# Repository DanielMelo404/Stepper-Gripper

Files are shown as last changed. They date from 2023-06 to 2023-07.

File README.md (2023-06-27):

# Stepper-Gripper
Three fingers gripper with stepper motor


\section{Estado del arte - BCI:}
Una interfaz cerebro-computador es el conjunto de hardware y software que permite controlar dispositivos externos con señales cerebrales \cite{RAMADAN201726}.
El origen de este campo de investigación sucede en 1924 con Berger, el cual hace el primer grabado de señales por electro encefalografia (EEG), e identifica el patrón oscilatorio, con las ondas alpha (8-13Hz).

\section{Objetivos actuales del campo:}
\begin{itemize}
    \item Mejorar la calidad de vida de personas con heridas o enfermedades que afectan su sistema nervioso.
    \item Conectar a los seres humanos con la inteligencia artificial con el objetivo de que esta no nos deje atrás (Neuralink).
\end{itemize}

\section{Diseño}

\subsection{Requerimientos funcionales}

\begin{enumerate}
    \item Poder ser controlada remotamente
    \begin{enumerate}[label*=\arabic*.]
        \item Debe poder conectarse facilmente con plataformas que la puedan controlar \\
        \textbf{DP: Node-red}
        \item Poder conectarse a internet \\
        \textbf{DP: ESP32 WROOM}
    \end{enumerate}
    \item Poder sujetar objetos de distintos tamaños
    \textbf{DP: Motor acoplado a tornillo de potencia que mueve axialmente al hexagono de presion}
    \begin{enumerate}[label*=\arabic*.]
        \item Poder sostener una fuerza de 20N para sujetar al objeto.\\
        \textbf{DP: El motor, junto al sistema de transmisión de potencia}
        \item Se debe poder controlar la posición de la mano en su rango de movimiento con una precision suficiente como para ejercer presion sobre los objetos en su rango de sujeción.\\
        \textbf{DP: Motor stepper que con definición de 200 pasos por vuelta}
        \item Debe permitir mover el hexágono de presión linealmente sobre su recorrido.\\
        \textbf{DP: Eje de motor acoplado a tornillo de potencia cuyo carro esta sujeto al hexágono de presión}
        \begin{enumerate}[label*=\arabic*.]
            \item Debe sujetar al motor rotatoriamente sobre su eje, ejerciendo un apoyo para que el motor ejerza su torque.\\
            \textbf{DP: Hexagono acrilico en la base del motor} 
            \item Debe sujetar al motor y al sistema axialmente para que sobre el se delice el hexagono de presion y sin ejercer un troque en contra que trabe al motor.\\
            \textbf{DP: Rodamiento de sujeción axial que encaja en escalon en la parte superior final del eje}
            
        \end{enumerate}
        
    \end{enumerate}
    \item El diseño debe ser usable

    \textbf{DP: Interfaz de usuario de node-red (dashboard) e instrucciones de uso}
    \item El diseño debe ser repetible
    \textbf{DP: Repositorio con los archivos necesarios para reproducción y el informe del presente documento}
\end{enumerate}

\section{Análisis geométrico del mecanismo:}
El mecanismo esta conformado por 3 mecanismos de 4 barras. Los 3 se controlan por medio de dos eslabones y una pieza triangular al hexágono de presión, el cual tiene un recorrido de 3cm desde la posición superior hacia abajo. Esta conexión hace girar alrededor de su eje pinado al eslabón de entrada del mecanismo de 4 barras y por medio de esto logra su movimiento.

El eslabón biela (el que se sujeta en sus extremos a los eslabones que giran alrededor de sus conexiones pinadas) del mecanismo es la misma pata de agarre que sujeta al objeto. 
Al transladarse por el movimiento axial del hexagono presion, este eslabon dismuye su "altura" y se cierra sobre la posicion de agarre. De esta manera sujeta al objeto.

\subsection{Análisis relativo a la mano humana} 

Cutkosky, basándose en el trabajo de Napier, desarrollo una clasificacion de movimientos funcionalmente estudiando las poses de las manos de maquinistas en operaciones de manufactura. Segun Napier, la mano adquiere una posicion deacuerdo a lo que quiere lograr con el objeto. 

La poses de la mano se clasifican entonces posiciones de potencia y de precisión.

El mecanismo esta diseñado para permitir efectuar2 posiciones de precisión: trípode y esférica.

En lo seres humanos, el agarre trípode se utiliza para elevar objetos pequeños, pues es preciso. Además, los 3 dedos virtuales que componen el agarre permiten ejercer 3 puntos fuerza lateral y momentos, los cual lo hace ideal para sujetar el movimiento de un objeto en una trayectoria cuyas fuerzas están en dirección alrededor de los 360 grados del gripper. Un ejemplo en humanos de esta tarea es la escritura con lápiz o desenroscar un objeto sosteniendolo de 3 lugares con los dedos.

El agarre esferico tambien forma parte de los agarres de potencia. Por medio de tener un punto de apoyo directo en el marco de la maquina (o en el efector de mayor potencia como el braso en el caso humano), el movimiento realizado ahora puede involucrar mucha mayor fuerza, pues los dedos que rodean al objeto no estan haciendo empuje sino que estan haciendo fuerza en direccion radial para sujetar al objeto. De esta manera, se puede controlar el movimiento de un objeto con mayor potencia que con el agarre de tripode.

Ambos agarres también tienen la ventaja de permitir el agarre de objetos de distintas formas y tamaños, pues no solo se pueden sujetar objetos esfericos o cilindricos sino tambien objetos rectangulares o de forma irregular.

Solo con realizar un cambio en la posicion de sujecion en node-red, se puede ajustar el mecanismo para sujetar distintos objetos. 

%uso de iot: Recibir datos de utilizacion del producto para saber como esta. 
% Flexibilidad: Que por medio de unos cambios pueda pasar de ser una protesis a ser un brazo para proposito de investigacion.
% O en la plataforma.

\begin{figure}[h]
    \centering
    \includegraphics[width = 7cm]{image.png}
    \caption{Orquidea que inicialmente es plana pero cambia su forma cuando entra en contacto con el agua \cite{youtube2}}
    \label{fig:my_label}
\end{figure}

\section{}

\section{KPIs de la mano:}

\subsection{Máxima carga sujetada-probeta:}
Tiene el objetivo de medir la capacidad de sujetar de la mano. Depende totalmente de la geometría del eslabón final de agarre y de el coeficiente de fricción de este con la pieza. \\

El procedimiento para se muestra a continuación. Este KPI esta medido respecto a una sola forma de probeta, con el material definido por el usuario de la mano. En este caso se utilizo un recipiente de plástico HDPE circular en el que se deposita la carga en el centro. 

\begin{enumerate}
    \item Se posiciona la mano directamente encima de la posición de agarre. De manera que solo se requiera un movimiento vertical para que la pieza quede entre las pinzas.
    \item Se baja la mano hasta la posición de sujeción en donde este el diámetro de sujeción de la probeta.
    \item Se realiza el movimiento de la mano hasta llegar a un punto cercano al objeto. Apartir de este punto, para el apriete, se realiza el movimiento del gripper con pasos discretos (enviando uno por uno). Se aprieta hasta antes de que el motor se deslice un paso. Si ya se deslizo, debe repetirse el apriete.
    \item Se eleva la mano verticalmente a una aceleración de menos de $1 cm/s^2$ hasta una altura de por lo menos 10cm.
    
\end{enumerate}

Si el anterior procedimiento fue exitoso, se toma el peso de la probeta utilizada como el valor de este KPI. Este KPI no solo consta del peso cargado sino también de la probeta utilizada (peso y forma).

Por esto se deben informar ambas informaciones al informar sobre este KPI.

\subsection{}
Este KPI busca medir la usabilidad de la mano, es decir, la facilidad con la que se puede realizar la función que desempeña. A este punto, la mano esta enfocada a poder hacer uso del sistema de actuación de la mano para hacer el testeo y verificación de este.\\
De esta forma, se define este KPI por medio de medir la cantidad de tiempo que le toma a una persona mover por primera vez la mano.

Metodología para la obtención de este KPI:

\begin{enumerate}
    \item La persona lee las instrucciones de utilización de la mano por completo.
    \item Se le indica a la persona que haga que el gripper se mueva y se toma el tiempo desde que se le indica esto hasta que mueve por primera vez la mano.
\end{enumerate}

Este KPI asume que la persona que lo utilizara es el laboratorista Juan Camilo de la universidad o cualquier persona que halla estudiado el pregardo en ingenieria Mecanica o Mecatronica que ya halla cursado los prerequisitos de la materia APM o materias equivalentes.

Tambien se asume que la persona sabe como acceder a node-red y tambien al dashboard de este.

\begin{itemize}
    \item 
\end{itemize}

\section{Gemelo digital}

El gemelo digital permite la simulación del mecanismo de la mano en su rango de movimiento. El método de reproducción de su geometría fue la medición de las medidas con calibrador con una resolución de 0.02mm. Los ángulos fueron medidos con el goniómetro disponible en el laboratorio con las medidas con una resolución de 1 grado.

\begin{figure}[h]
    \centering
    \includegraphics[width = 7cm]{twin.png}
    \caption{Gemelo digital de la mano \cite{youtube2}}
    \label{fig:my_label}
\end{figure}

Así mismo el gemelo digital se verifico al imprimir las piezas en material PLA. Se encontraron desviaciones respecto a las dimensiones principales de \pm 1.3mm.

\begin{figure}[h]
    \centering
    \includegraphics[width = 7cm]{dash.png}
    \caption{Interfaz de usuario node-red \cite{youtube2}}
    \label{fig:my_label}
\end{figure}

El gemelo digital permite la simulacion del movimiento del mecanismo, lo cual sera util para previsualizar el movimiento del actuador una vez armado.

\section{IIoT}

\subsection{Conexion wifi}

El ESP32 utiliza las credenciales de la red, nombre de la red y contraseña de esta, para conectarse al inicio de su funcionamiento.
Las credenciales se ingresan directamente en el codigo del ESP32.

\begin{figure}[h]
    \centering
    \includegraphics[width = 7cm]{wifi.png}
    \caption{Conexion wifi}
    \label{fig:my_label}
\end{figure}

\subsection{Conexion MQTT}
El esquema de conexion se puede apreciar en el diagrama POA estatico. El ESP32 se conecta gracias a la libreria PubSubClient con el broker MQTT de hive. Alli crea un topico llamado StepperDMAOut y publica a este topico. Tambien se subsribe a un topico llamado stepperDMAin, a donde se envia la posicion del actuador.    

El servidor de Node-red, instaldo en alguna raspberry-pi o computador con conexion a internet, publica la informacion de posicion del actuador al topico stepperDMAin y se subscribe al topico stepperDMAout, del mismo borker Hive.

\begin{figure}[h]
    \centering
    \includegraphics[width = 7cm]{conect.png}
    \caption{Codigo para conexion con broker}
    \label{fig:my_label}
\end{figure}

\begin{figure}[h]
    \centering
    \includegraphics[width = 7cm]{node.png}
    \caption{Diagrama de node-red utilizado para la conexion con el broker}
    \label{fig:my_label}
\end{figure}

La informacion del usuario se captura por medio de los nodos slider y numeric, los cuales representan componentes de la interfaz de usuario en el dashboard de nodered.

\begin{figure}[h]
    \centering
    \includegraphics[width = 7cm]{node.png}
    \caption{Dashboard de node-red}
    \label{fig:my_label}
\end{figure}

La conexion con el broker MQTT se realiza por medio de los nodos receptor y publicador, los cuales utilizan la informacion de la direccion del broker, el nombre de los topicos y el puerto de este para realizar la conexion.

El dato enviado desde node red es la carga paga, la cual tiene el tipo de dato payload. Al llegar y salir del borker sale con tipo byte y en el ESP 32 se realiza su conversion a char y luego a int, para asi finalmentes ser utilizada como el numero de pasos que el motor dara desde su posicion de inicio.

La posicion de inicio corresponde a 0 pasos. Por esto la posicion del hexagono de presion debe comenzar desde el principio del recorrido del tornillo de potencia, en la parte superior.

\section{Electrónica y control del motor}

El circuito se compone del ESP32 y del driver del motor stepper. Tambien se utiliza un regulador de 5V para darle poder al ESP32, un capacitor de desacople para compensar cambios de corriente bruscos, y unos leds indicadores. Las borneras se utilizan para conectar con el motor y la bornera-conector para conectar la fuente de 12V.

El control del motor se realizo por medio de los pines step y dir. Una vez conectado el driver como se oberva en la figUra \cite{4988}, el pin step se debe conectar a algun GPIO del ESP32. Puede ser cualquiera pero se utilizo el GPIO 1. Cada vez que el motor da un paso, se envia un pulso por este pin. El pin dir se utiliza para controlar la direccion del motor. Tambien se puede conectar a cualquier GPIO pero se utilizo el GPIO 3.

\begin{figure}[h]
    \centering
    \includegraphics[width = 7cm]{a4988.png}
    \caption{Esquema de conexión para el driver}
    \label{4988}
\end{figure}

El circuito se manufacturo per medio de serigrafia en PCB y los archivs de Kicad se encuentran disponbiles en el repositorio "stepper gripper" de github. 

\begin{figure}[h]
    \centering
    \includegraphics[width = 7cm]{squema.png}
    \caption{Esquematico del circuito}
    \label{fig:my_label}
\end{figure}

\begin{figure}[h]
    \centering
    \includegraphics[width = 7cm]{circu.png}
    \caption{Circuito en PCB}
    \label{fig:my_label}
\end{figure}

\section{Control del movimiento del motor}

El control de movimiento se realizo por medio de la libreria accelstepper de Arduino. 

Se debe instanciar una interfaz de stepper indicando los pines de pasos y dirección. \cite{int}

\begin{figure}[h]
    \centering
    \includegraphics[width = 7cm]{acc.png}
    \caption{Instanciación de interfaz para motor}
    \label{int}
\end{figure}

El setup del stepper se muestra en la figura \cite{in2}. 
Estos parametros se utilzran cuando sele solicite al motor alcanzar una posicion. setAcceleration configura la aceleracion para el perfil trapezoidal que siguie el stepper entre posicion y posicion. La velocidad maxima durante recorrido trapezoidal tambien se cofigura con setMaxSpeed.

setSpeed se utiliza para configurar la velocidad a la que el motor se movera cuando lo haga a velocidad constante sin aceleracion o desaceleracion.

\begin{figure}[h]
    \centering
    \includegraphics[width = 7cm]{set.png}
    \caption{Establecimiento de parámetros iniciales para motor}
    \label{int2}
\end{figure}

El motor se controla en el ciclo loop por medio del codigo de la figura \ref{in3}. Requested position es la posicion solicitada y reachingPosition es la posición a la que se esta moviendo en ese momento en particular.
Si estas son distintas, se realiza el comando moveTo, el cual interrumpe el movimiento y hace que el motor inmediatamente comience a moverse hacia la posición señalada.

\begin{figure}[h]
    \centering
    \includegraphics[width = 7cm]{mot.png}
    \caption{Establecimiento de parámetros iniciales para motor}
    \label{in3}
\end{figure}

\section{Algoritmo de clasificación de señales}

\begin{figure}[h]
    \centering
    \includegraphics[width = 7cm]{mot.png}
    \caption{Establecimiento de parámetros iniciales para motor}
    \label{in3}
\end{figure}

\begin{figure}[h]
    \centering
    \includegraphics[width = 7cm]{mot.png}
    \caption{Establecimiento de parámetros iniciales para motor}
    \label{in3}
\end{figure}

El algoritmo 

\section{Conclusiones:} \label{sec:metodologia} %10min

\begin{itemize}
    \item La manufactura aditiva es poderosa cuando es utilizada en conjunto con un gemelo digital por medio de permitir la reproducción exacta de la pieza y de esta forma desacoplando el proceso de prototipado del objeto real.
    \item Node-red facilita la conexión con protocolo MQTT con borkers, por medio de la representación intuitiva con nodos y flujos del sistema de información
    \item Los motores steppers facilitan el control de movimiento por medio de no requerir un sistema de feedback para controlar su posición y al permitir un torque sostenido.
\end{itemize}

\begin{itemize}
   
\end{itemize}

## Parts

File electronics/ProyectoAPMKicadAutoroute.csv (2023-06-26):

# | Reference | Qty | Value | Footprint | DNP
1 | C1 | 1 | 100u | Capacitor_THT:CP_Axial_L10.0mm_D6.0mm_P15.00mm_Horizontal
2 | J1, J2 | 2 | Conn_01x15_Socket | Connector_PinSocket_2.54mm:PinSocket_1x15_P2.54mm_Vertical
3 | J3, J4 | 2 | Conn_01x08_Socket | Connector_PinSocket_2.54mm:PinSocket_1x08_P2.54mm_Vertical
4 | J5, J6, J7 | 3 | Screw_Terminal_01x02 | TerminalBlock:TerminalBlock_Altech_AK300-2_P5.00mm
5 | J8 | 1 | PicKit | Connector_PinHeader_2.54mm:PinHeader_1x05_P2.54mm_Vertical
6 | J9 | 1 | PicKit | Connector_PinHeader_2.54mm:PinHeader_1x01_P2.54mm_Vertical
7 | R1, R2 | 2 | 330 | Resistor_THT:R_Axial_DIN0204_L3.6mm_D1.6mm_P7.62mm_Horizontal
8 | U1 | 1 | LM7805_TO220 | Package_TO_SOT_THT:TO-220-3_Horizontal_TabDown

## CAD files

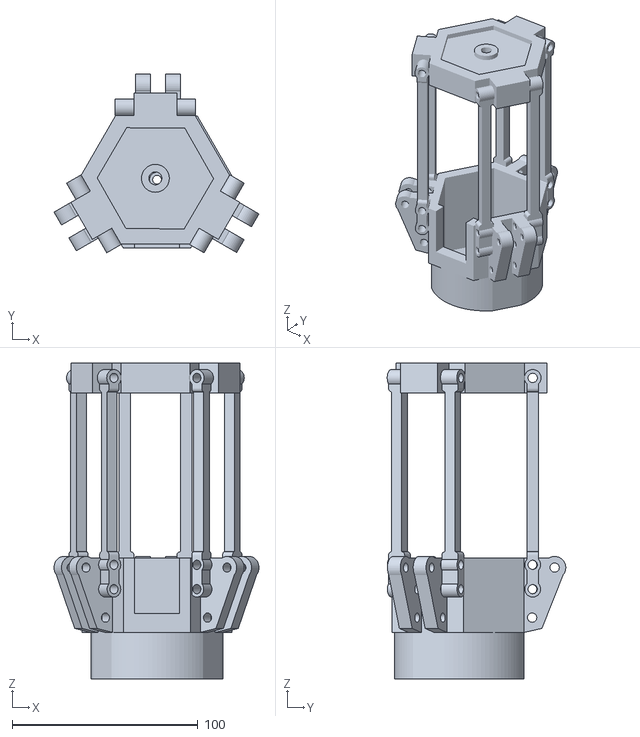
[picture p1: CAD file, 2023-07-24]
3D models/STLfiles/marco_ensamblado.stl
110.2 x 96.0 x 169.9

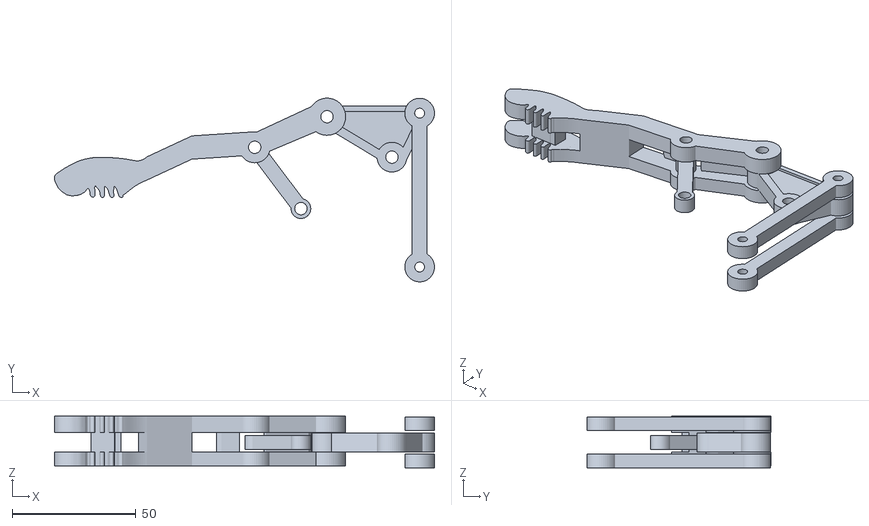
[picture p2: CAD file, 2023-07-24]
3D models/STLfiles/subensamble_patas.stl
153.4 x 74.2 x 20.9

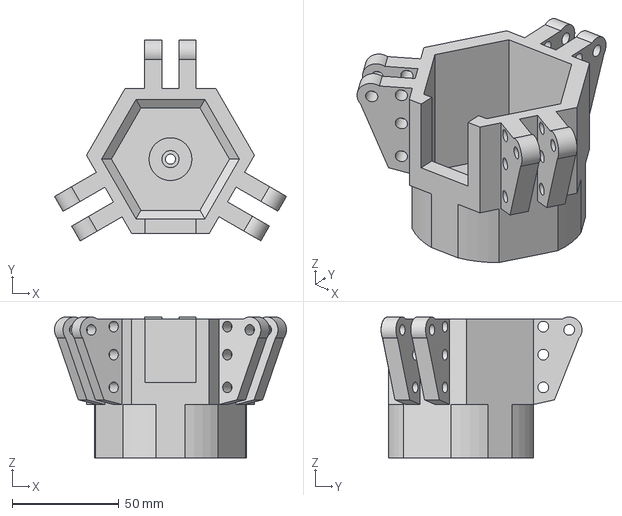
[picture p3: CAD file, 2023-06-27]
3D models/Marco v13.step
108.5 x 94.0 x 65.9 mm

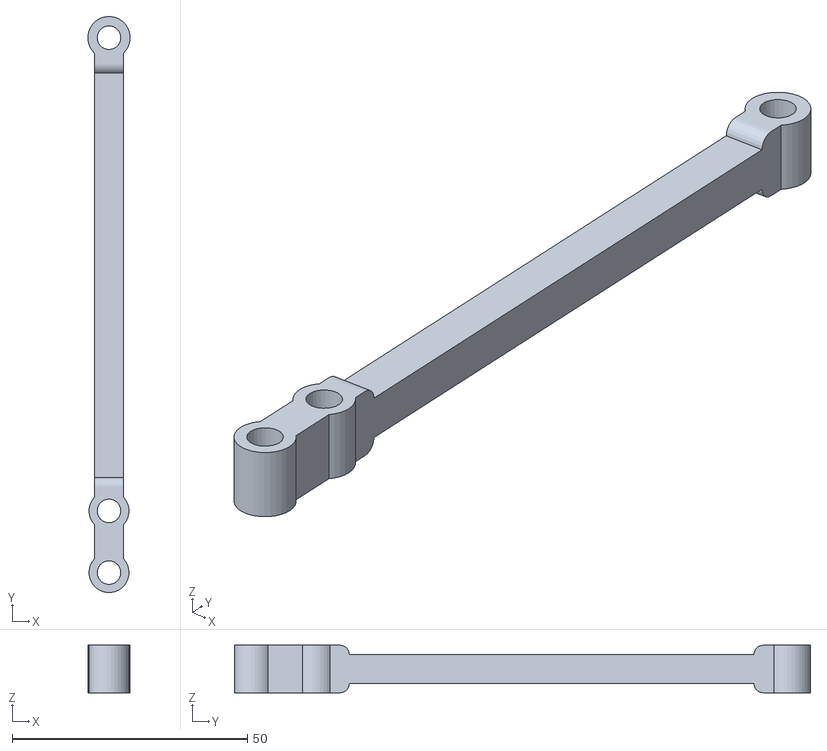
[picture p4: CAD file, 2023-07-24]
3D models/STL_en_metros/Barra_marco_en_m.stl
8.97 x 122.3 x 10.1

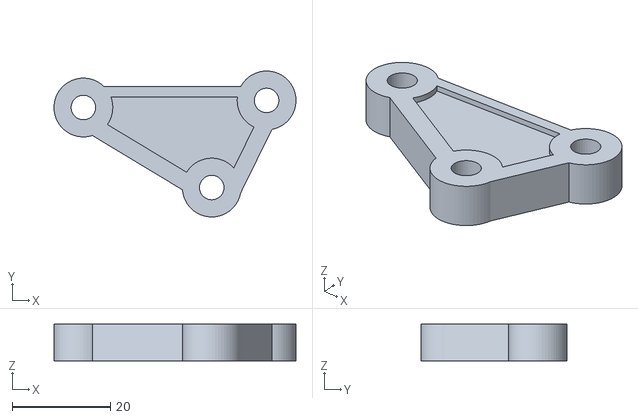
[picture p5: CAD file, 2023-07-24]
3D models/STLfiles/triangulo.stl
49.4 x 29.8 x 7.50

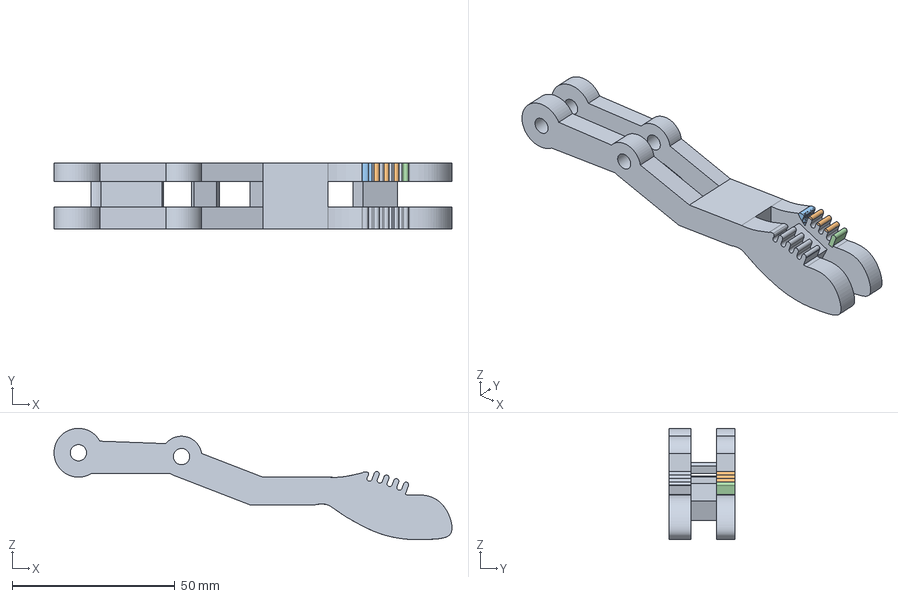
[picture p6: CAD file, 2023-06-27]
3D models/Pata de agarre (v14~recovered).step
122.3 x 20.1 x 34.2 mm

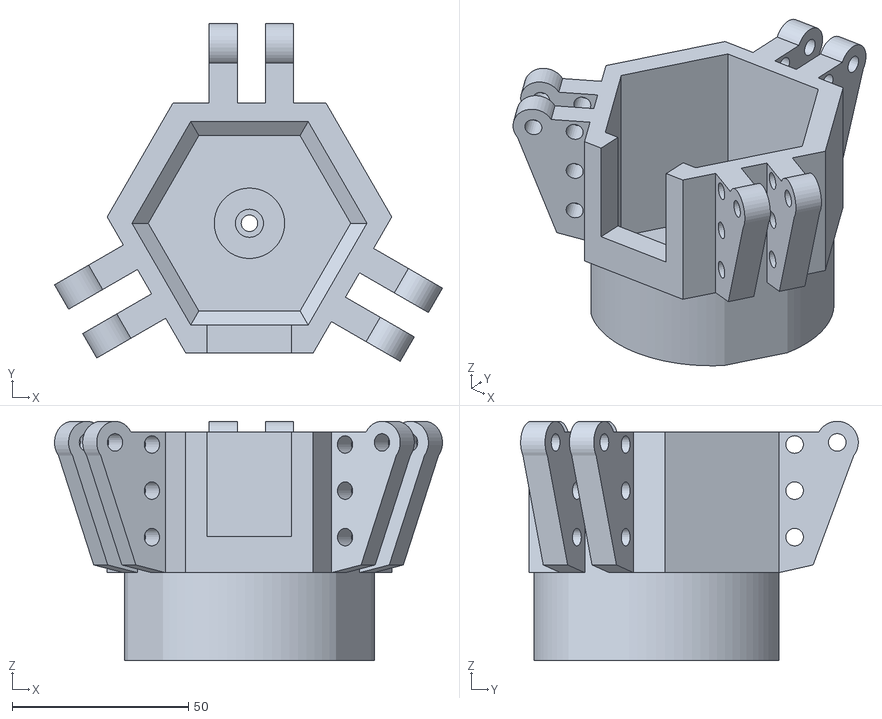
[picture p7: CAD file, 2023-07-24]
3D models/STLfiles/Marco.stl
110.2 x 95.9 x 68.0

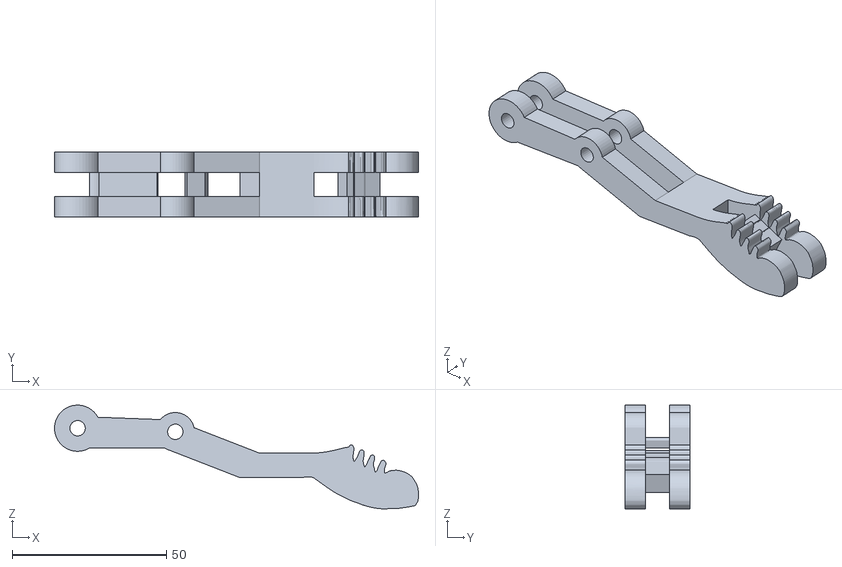
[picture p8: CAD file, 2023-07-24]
3D models/STLfiles/Pata_de_agarre.stl
118.0 x 21.2 x 33.6

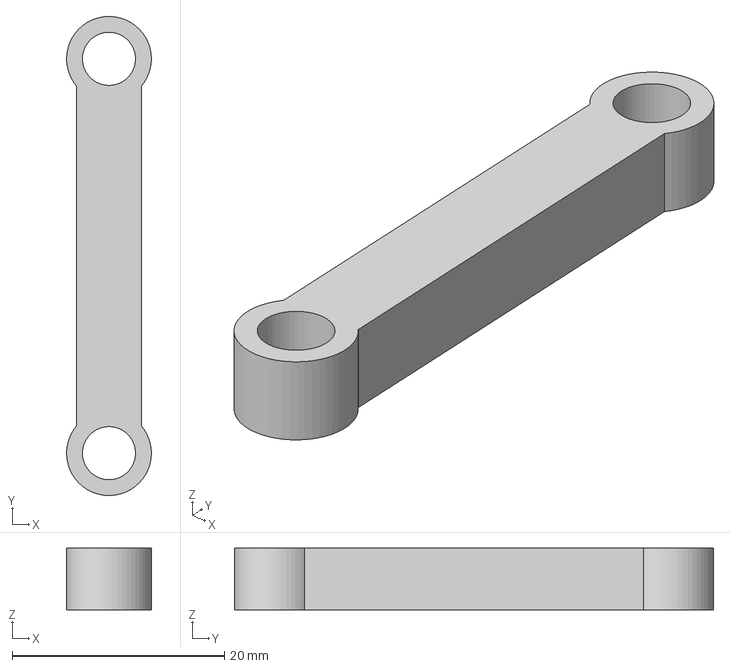
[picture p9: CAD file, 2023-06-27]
3D models/Eslabon pequeño v5.step
8.00 x 45.2 x 5.80 mm

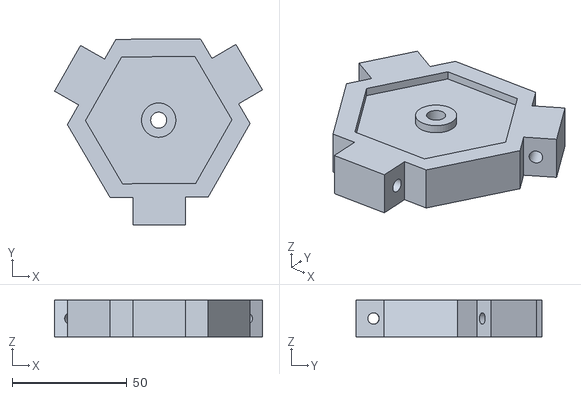
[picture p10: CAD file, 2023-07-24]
3D models/STLfiles/Hexagono_superior.stl
90.8 x 81.4 x 16.0

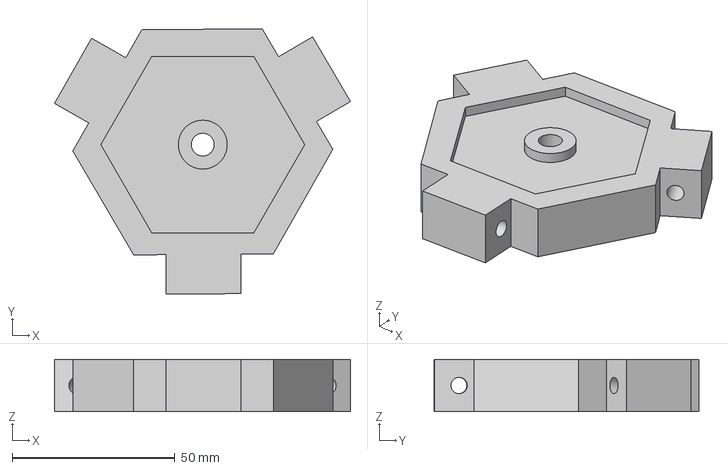
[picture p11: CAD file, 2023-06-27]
3D models/Hexagono superior con rodamiento v12.step
90.8 x 81.4 x 16.0 mm

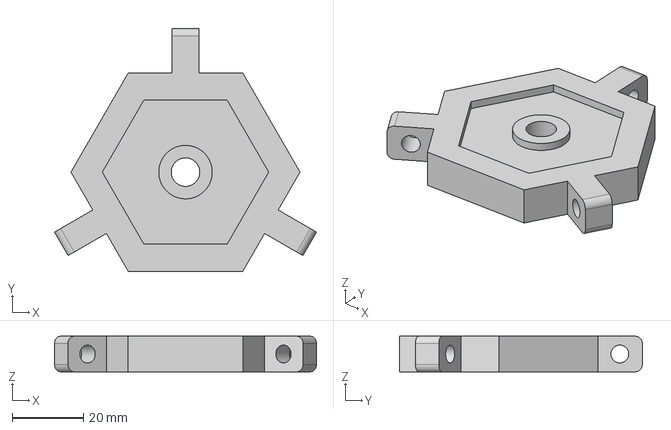
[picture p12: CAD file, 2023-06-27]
3D models/Hexagono de presion original v1.step
73.4 x 68.0 x 10.0 mm

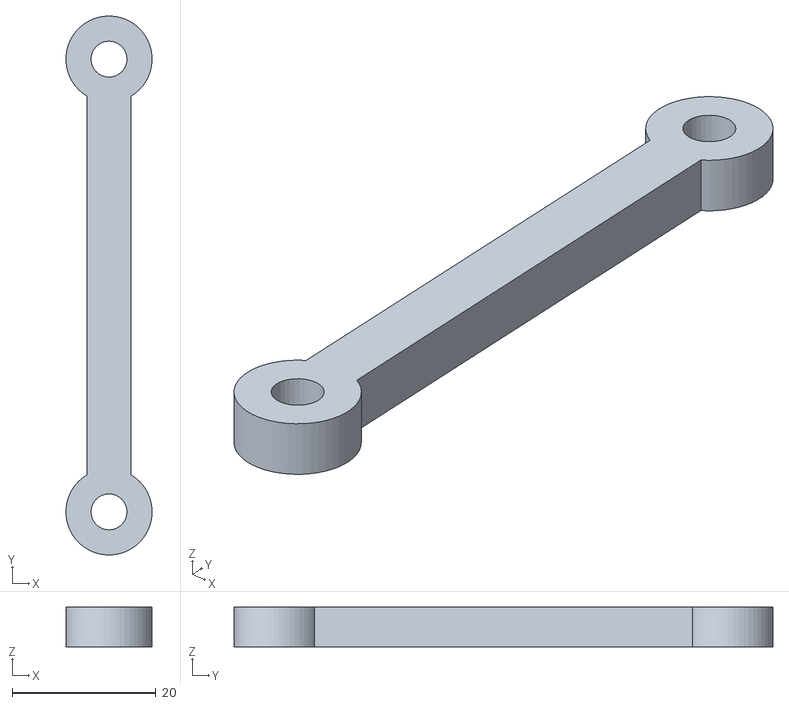
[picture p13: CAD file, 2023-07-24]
3D models/STLfiles/Eslabon_esbelto.stl
12.0 x 75.0 x 5.50

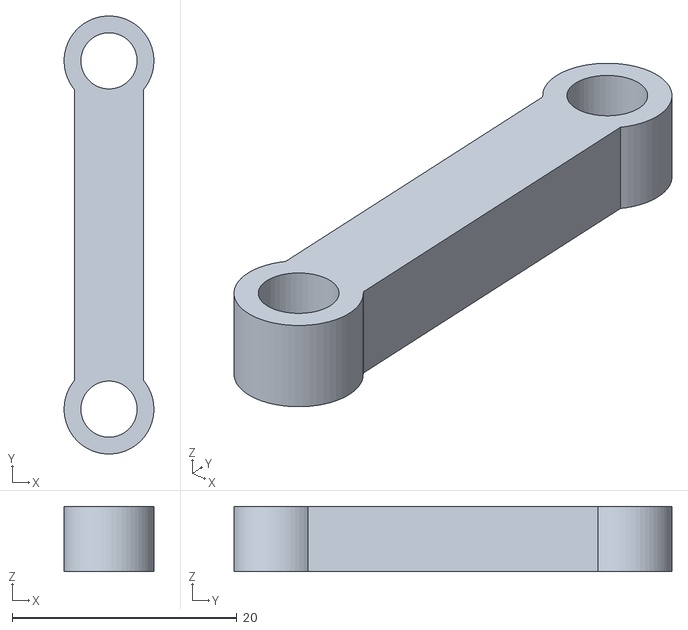
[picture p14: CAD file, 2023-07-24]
3D models/STLfiles/Eslabon_pequeño.stl
7.99 x 39.0 x 5.80

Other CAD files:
3D models/Barra marco v8.step
3D models/STLfiles/Hexagono_de_presion.stl
3D models/ensamble v16.f3z

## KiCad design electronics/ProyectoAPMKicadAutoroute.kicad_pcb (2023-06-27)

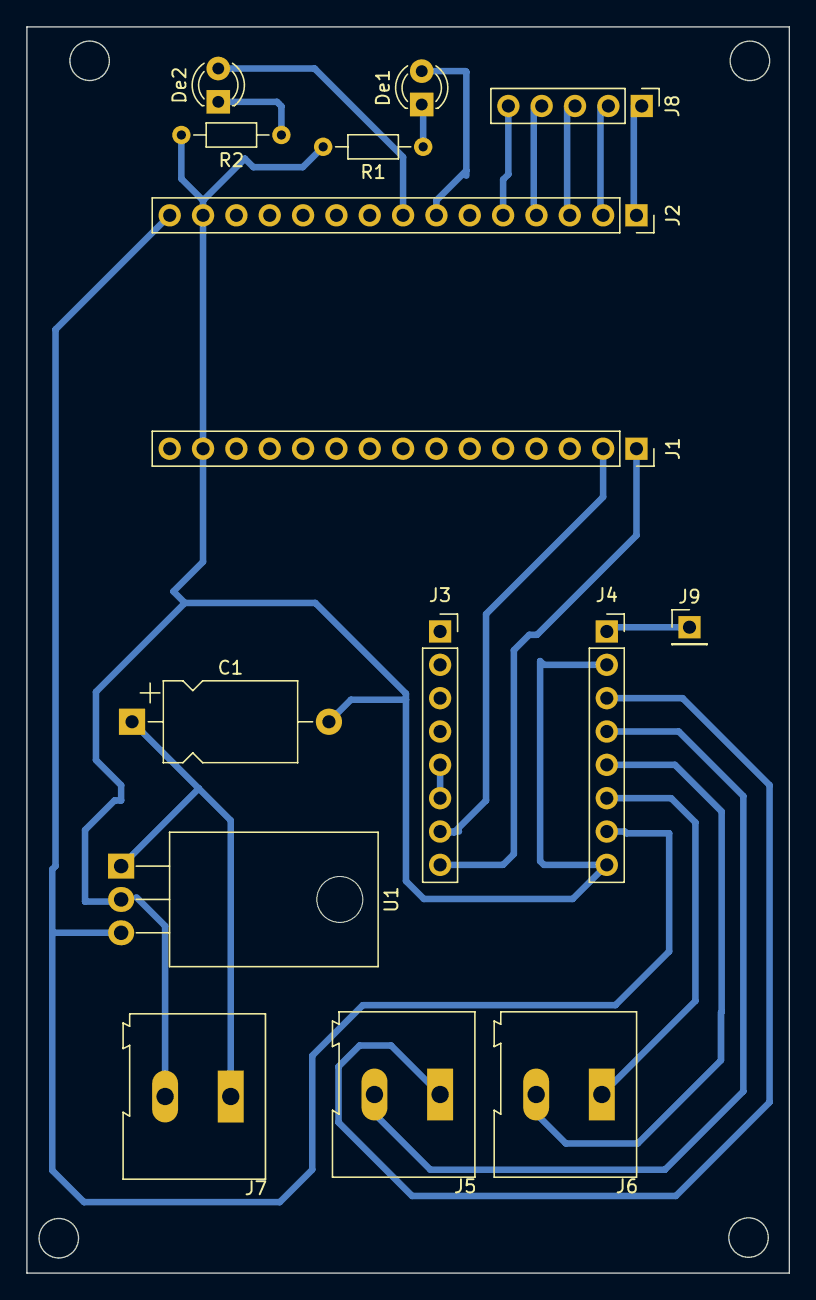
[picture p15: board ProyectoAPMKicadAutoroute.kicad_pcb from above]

Board: 2 copper layers, 58.1 x 94.9 mm, 15 parts (0 on the bottom side), 20 nets.

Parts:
C1: 100u; CP_Axial_L10.0mm_D6.0mm_P15.00mm_Horizontal
De1, De2: LED; LED_D3.0mm_Clear
J1, J2: Conn_01x15_Socket; PinSocket_1x15_P2.54mm_Vertical
J3, J4: Conn_01x08_Socket; PinSocket_1x08_P2.54mm_Vertical
J5, J6, J7: Screw_Terminal_01x02; TerminalBlock_Altech_AK300-2_P5.00mm
J8: PicKit; PinHeader_1x05_P2.54mm_Vertical
J9: PicKit; PinHeader_1x01_P2.54mm_Vertical
R1, R2: 330; R_Axial_DIN0204_L3.6mm_D1.6mm_P7.62mm_Horizontal
U1: LM7805_TO220; TO-220-3_Horizontal_TabDown

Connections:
12V+: C1.1, J7.1, U1.1 (VI)
GND: C1.2, J1.14, J2.14, J4.2, J4.8, J7.2, R1.2, R2.2, U1.2 (GND)
unnamed: De1.2 (A), J2.7
unnamed: De1.1 (K), R1.1
unnamed: De2.2 (A), J2.8
unnamed: De2.1 (K), R2.1
unnamed: J2.1, J8.1
unnamed: J2.2, J8.2
unnamed: J2.3, J8.3
unnamed: J2.4, J8.4
unnamed: J2.5, J8.5
unnamed: J3.5, J3.6
unnamed: J4.1, J9.1
unnamed: J4.3, J5.1
unnamed: J4.4, J5.2
unnamed: J4.5, J6.2
unnamed: J4.6, J6.1
VDD: J2.15, J4.7, U1.3 (VO)
dir: J1.1, J3.8
step: J1.2, J3.7

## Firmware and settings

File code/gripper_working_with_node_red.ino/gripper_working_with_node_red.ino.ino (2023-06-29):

/*
 Basic ESP8266 MQTT example
 This sketch demonstrates the capabilities of the pubsub library in combination
 with the ESP8266 board/library.
 It connects to an MQTT server then:
  - publishes "hello world" to the topic "outTopic" every two seconds
  - subscribes to the topic "inTopic", printing out any messages
    it receives. NB - it assumes the received payloads are strings not binary
  - If the first character of the topic "inTopic" is an 1, switch ON the ESP Led,
    else switch it off
 It will reconnect to the server if the connection is lost using a blocking
 reconnect function. See the 'mqtt_reconnect_nonblocking' example for how to
 achieve the same result without blocking the main loop.
 To install the ESP8266 board, (using Arduino 1.6.4+):
  - Add the following 3rd party board manager under "File -> Preferences -> Additional Boards Manager URLs":
       http://arduino.esp8266.com/stable/package_esp8266com_index.json
  - Open the "Tools -> Board -> Board Manager" and click install for the ESP8266"
  - Select your ESP8266 in "Tools -> Board"
*/
#include <stdlib.h>
#include <WiFi.h>
#include <PubSubClient.h>
#include <AccelStepper.h>
#define BUILTIN_LED 2


const int dirPin = 1;
const int stepPin = 3;
//const int en = 3;
const int ms1 = 21;
const int ms2 = 19;
const int ms3 = 18;
const int reset = 5;
const int sleepPin = 17;


void setupPins(){
//  digitalWrite(en, LOW);
  digitalWrite(ms1, LOW);
  digitalWrite(ms2, LOW);
  digitalWrite(ms3, LOW);
  digitalWrite(reset, HIGH);
  digitalWrite(sleepPin, HIGH);
//  digitalWrite(en, LOW);
}

int requestedPosition =0;
int reachingPosition = 0;

// Define motor interface type
#define motorInterfaceType 1

AccelStepper myStepper(motorInterfaceType, stepPin, dirPin);

// Update these with values suitable for your network.

const char* ssid = "wifiName";
const char* password = "wifiPassword";

const char* mqtt_server = "broker.hivemq.com";

WiFiClient espClient;
PubSubClient client(espClient);
unsigned long lastMsg = 0;
#define MSG_BUFFER_SIZE  (50)
char msg[MSG_BUFFER_SIZE];
int value = 0;

void setup_wifi() {

  delay(10);
  // We start by connecting to a WiFi network
  Serial.println();
  Serial.print("Connecting to ");
  Serial.println(ssid);
  WiFi.mode(WIFI_STA);
  WiFi.begin(ssid, password);

  while (WiFi.status() != WL_CONNECTED) {
    delay(500);
//    Serial.print(".");
  }

  randomSeed(micros());

//  Serial.println("");
//  Serial.println("WiFi connected");
//  Serial.println("IP address: ");
//  Serial.println(WiFi.localIP());
}

void callback(char* topic, byte* payload, unsigned int length) {
//  Serial.print("Message arrived [");
//  Serial.print(topic);
//  Serial.print("] ");
  char pos[length];
  for (int i = 0; i < length; i++) {
    pos[i] = (char)payload[i];
//    Serial.print((char)payload[i]);
  }
  Serial.println(pos);
char *output;
    long result = strtol(pos, &output, 10) + 1;
//Serial.println((int)result);
//  requestedPosition = ((char)payload[0]-'0')*100;
requestedPosition = -1*(int)result;

//  Serial.println("requestedPosition"+(String)requestedPosition);
//Serial.println((char)payload[0]);

  
//  Serial.println();

  // Switch on the LED if an 1 was received as first character
  if ((char)payload[0] == '1') {
    digitalWrite(BUILTIN_LED, LOW);   // Turn the LED on (Note that LOW is the voltage level
    // but actually the LED is on; this is because
    // it is active low on the ESP-01)
  } else {
    digitalWrite(BUILTIN_LED, HIGH);  // Turn the LED off by making the voltage HIGH
  }
}

void reconnect() {
  // Loop until we're reconnected
  while (!client.connected()) {
    Serial.print("Attempting MQTT connection...");
    // Create a random client ID
    String clientId = "ESP8266Client-";
    clientId += String(random(0xffff), HEX);
    // Attempt to connect
    if (client.connect(clientId.c_str())) {
      Serial.println("connected");
      // Once connected, publish an announcement...
      client.publish("outTopicDMA", "hello world");
      // ... and resubscribe
      client.subscribe("stepperDMAtopic");
    } else {
      Serial.print("failed, rc=");
      Serial.print(client.state());
      Serial.println(" try again in 5 seconds");
      // Wait 5 seconds before retrying
      delay(5000);
    }
  }
}



void setup() {
  pinMode(BUILTIN_LED, OUTPUT);     // Initialize the BUILTIN_LED pin as an output
//  Serial.begin(115200);
  setup_wifi();

setupPins();
//  Setup stepper
  myStepper.setMaxSpeed(500);
//  myStepper.setAcceleration(20);

    myStepper.setMinPulseWidth(55); 
//  Serial.begin(9600);

myStepper.setSpeed(500);
myStepper.moveTo(requestedPosition);
myStepper.setSpeed(500);

pinMode(18,OUTPUT);
  client.setServer(mqtt_server, 1883);
  client.setCallback(callback);
}

void loop() {
//  Serial.println(requestedPosition);
//  Serial.println("hi");
    if (requestedPosition != reachingPosition){
    reachingPosition = requestedPosition;
    myStepper.moveTo(requestedPosition);
    if(requestedPosition <myStepper.currentPosition() ){
        myStepper.setSpeed(-500);
    
    }else{
       myStepper.setSpeed(500);
    }
//    Serial.println((String)myStepper.currentPosition());
    
  }
  if (myStepper.currentPosition() == requestedPosition){
    myStepper.stop();
//    Serial.print("stop" + (String)myStepper.currentPosition());
  }
  else{
    myStepper.runSpeed();
  }

  
  if (!client.connected()) {
    reconnect();
  }
  client.loop();

//  unsigned long now = millis();
//  if (now - lastMsg > 20000) {
//    lastMsg = now;
//    ++value;
////    snprintf (msg, MSG_BUFFER_SIZE, "hello world #%ld", value);
////    Serial.print("Publish message: ");
////    Serial.println(msg);
//    client.publish("outTopicDMA", msg);
//  }
}
